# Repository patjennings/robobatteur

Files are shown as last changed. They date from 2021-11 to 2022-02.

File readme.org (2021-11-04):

* Robobatteur
** Principes
   Suite au travail sur la première version du robobatteur, qui effectuait un simple "poum-tchac", j'ai réfléchi à une version plus évoluée.

   La principale évolution sera de pouvoir contrôler le robot à partir d'une séquence midi. Un séquenceur MIDI jouera une partition, et enverra à mesure qu'elle joue des messages aux moteurs. Voici le schéma de principe : sur la ligne du haut, les éléments par lesquels le message passe, sur celle du bas, le message

   #+begin_src text
Ordi -------> Midi out (carte son) --> Midi in (circuit) --> carte Arduino -------------------> circuit --> servomoteur
Note MIDI -------------------------------------------------> routage / instructions de frappe ------------> frappe
   #+end_src

   Cela engendre une autre modification sur la machine, afin de pouvoir assurer la frappe sur des tempos élevés. 2 moteurs par élément, qui farppent alternativement.

   Chaque note correspond à un élément. La note 30 (Do 1) correspond à la grosse caisse, la note 32 à la caisse claire, etc. Les notes sont récapitulées dans le tableau ci-dessous.

   J'ai prévu de pouvoir contrôler quatre éléments de batterie.
   
   | Note MIDI | Note | Élément |
   |-----------+------+---------|
   |        43 | G1   | Ride    |
   |        42 | F1   | Hi-hat  |
   |        38 | D1   | Snare   |
   |        36 | C1   | Kick    |
   
   On s'appuie toujours sur une carte Arduino Uno pour effectuer ce travail.
   
** Circuit
   Plusieurs besoins pour le circuit :
   - un midi in
   - une alimentation par groupe de servos dédiés (les servos ont besoin chacun d'une intensité d'un ampère pour fonctionner correctement. Comme il est difficile de se procurer du 5V 8A, pour pallier à cela, on n'alimente que deux moteurs avec une seule alim 5v à 2a).

   J'ai utilisé une perfboard pour le circuit du module de MIDI In et pour le câblage des servo moteurs, et une autre board pour les circuits d'alim des servos. J'ai fait ça à mesure que j'avancais, j'imagine qu'il y a moyen d'optimiser ça.

   Comme je l'ai mentionné plus haut, j'ai besoin de taper sur quatre éléments de batterie : j'aurai donc besoin de huit servomoteurs.

   #+html: <img src="docs/robobatteur_bb.jpg" width="100%"/>
   
** Menuiserie, disposition
   Principe général. Tout sur un socle, qu'on peut lester avec des parpaings. La disposition reprend celle d'une batterie jouée par un humain, à savoir grosse caisse au milieu, et charleston et caisse claire de part et d'autre.
   Mais on peut être plus ambitieux et disposer ses éléments dans l'espace : après tout, on est seulement limité par la longueur de câble
   Bras dont on peut modifier la rotation, afin de pouvoir effectuer des ajustements fins, pour avoir une frappe assez sonore.
   
   Fixation des servos : baguette en pin (16mm), percé pour recevoir le moteur. Fixation avec des vis
   Fixation des baguettes : perçage, puis fixation avec vis dans le bras de chaque servo
   
   Le circuit et la carte sont fixés dans une boîte, d'où partent les câbles vers les servos (8 groupe de 3 câbles ― phase, neutre, message arduino (?))

   Les câbles sont fixés. C'est encore à l'état de prototype "early", et la robustesse de connexions est le prochain point que je compte améliorer.
   
** Code
   Le code est relativement simple. Les variables sur lesquelles on jouera en fonction du montage sont dans initPos[]. L'angle de rotation de chaque baguette est défini par rotationAngle. On pourra peut-être jouer avec. J'ai peu testé, mais on gagne peut-être en puissance. Le code se répète pas mal, et il pourrait aisément être factorisé. Cela est dû à mes compétences limitées. Malgré tout, le code est sûrement plus lisible pour des novices qui tâcheraient de comprendre ce qui se passe.

*** Librairies externes
    Le programme s'appuie sur les librairies ~MIDI~ et ~Servo~.

    Comment les télécharger ? Le plus simple est d'utiliser l'IDE Arduino, est d'installer les modules via le menu ~Menu~.

    #+html: <img src="docs/lib-install.png"/>

    La librairie ~MIDI~
    #+html: <img src="docs/lib-midi.png"/>

    La librairie ~Servo~
    #+html: <img src="docs/lib-servo.png"/>
    
    Une fois installées, on appelle les librairies dans le code :

    #+begin_src c
     #include <MIDI.h>  // Add Midi Library
     #include <Servo.h> // Add servo lib
    #+end_src

** Fichiers MIDI
   Les fichiers MIDI sont créés avec ~Rosegarden~. J'ai pu tester avec des (croches, doubles-croches) à un tempo de (combien) ?
   
** Setup informatique
   ~QJackCtl~ + ~a2jmidid~ + ~Rosegarden~

   J'utilise Linux Mint. Le setup sera à adapter en fonction de l'OS, et sera sûrement plus simple dans d'autres environnements. Quoi qu'il en soit, voici le mien :

   Les applications utilisées sont :
   - ~QJackCtl~ pour piloter la carte son et effectuer les connexions
   - ~a2jmidid~ pour envoyer des messages MIDI via la carte son
   - ~Rosegarden~ pour créer et lire les fichiers MIDI

   Rosegarden ferta tourner les séquences midi, et enverra les notes vers la carte son via ~QJackCtl~ et ~a2jmidid~ (qui permet à ~QJackCtl~ de piloter les connexions midi).

   #+begin_src bash
     sudo apt-get update
     sudo apt-get install -y qjackctl a2jmidid rosegarden
   #+end_src
   
   Une carte son (/Presonus Audibox44VSL/ pour ma part) est connectée en USB à l'ordinateur.
   
   Ensuite, ~QJackCtl~ est démarré. Si tout roule, on peut lancer ~a2jmidid~

   #+begin_src bash
     a2jmidid -e
   #+end_src

   Si tout fonctionne, on doit voir quelque chose comme ça

   #+begin_src bash
   Retour terminal
   #+end_src

   Puis on peut démarrer ~Rosegarden~

   Une fois que tout est démarré, on revient dans les connexions de ~Qjack~ pour vérifier que ~RoseGarden~ envoie des messages vers le midi out de la carte son (grâce à ~a2jmidid~)

   Si tout fonctionne correctement, une note lue sur ~Rosegarden~ doit activer les servo moteurs

** Améliorer
   Précision des fixations  : angle de fixation des baguettes et des servos aléatoires, ce qui nuit à l'exactitude du tempo (rubato).
   
** Matériel
- Assortiment de fils : <https://www.lextronic.fr/assortiment-fils-de-cablage-monobrin-30m-62595.html>
- Perfboard : <https://www.lextronic.fr/plaque-a-pastilles-cuivrees-81x51-mm-31761.html>
- Condensateur 100 µF <https://www.lextronic.fr/condensateur-chimique-radial-1000uf-35v-58165.html#/condensateurs_85-100f_10v>
- Embase 5v : <https://www.lextronic.fr/embase-d-alimentation-2-1x5-5mm-2529.html>
- Embase DIN : me souviens plus
- Alimentation : 5v 2a (chez RS Composants)
- Servo moteur MG996R : <https://www.miniplanes.fr/servos/tower-pro/mg-996-servo-numerique-pignons-metaux-10kgcm-tower-pro-p-19942.html>
- Résistance 220 ohms + 4.7kohms
- Diode : 1n914 ou 1n4148 <https://composant-electronique.fr/diode-1n4148>
- Optocoupleur 6n138 : <https://composant-electronique.fr/optocoupleur-6n138>

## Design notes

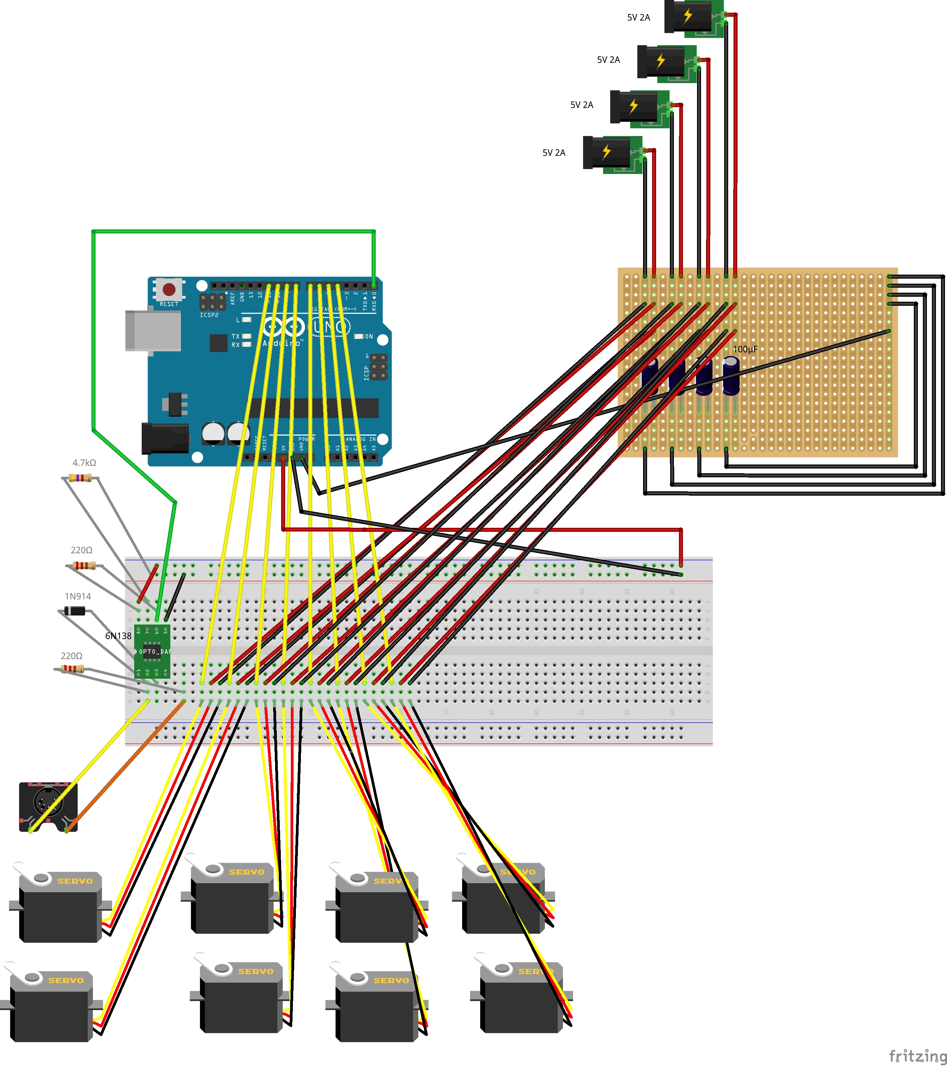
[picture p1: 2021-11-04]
docs/robobatteur_bb.jpg

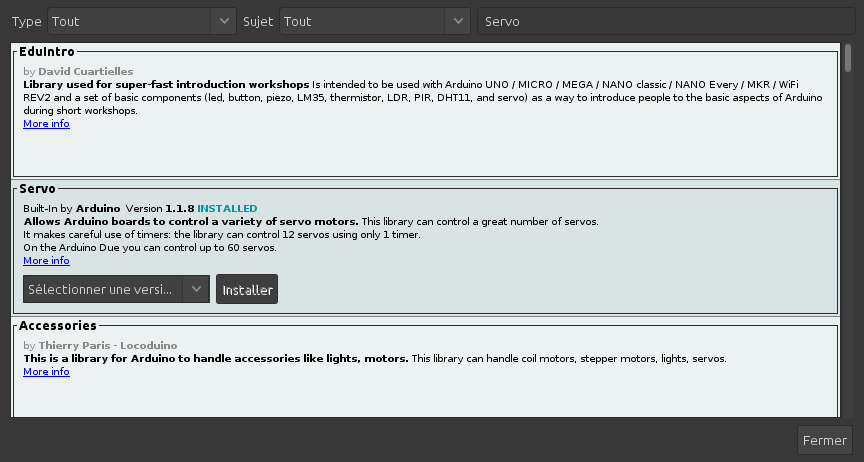
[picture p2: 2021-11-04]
docs/lib-servo.png

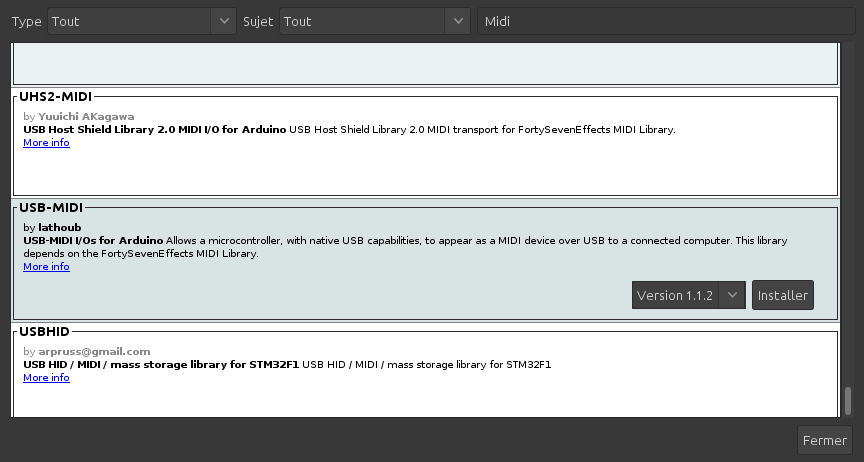
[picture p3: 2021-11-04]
docs/lib-midi.png

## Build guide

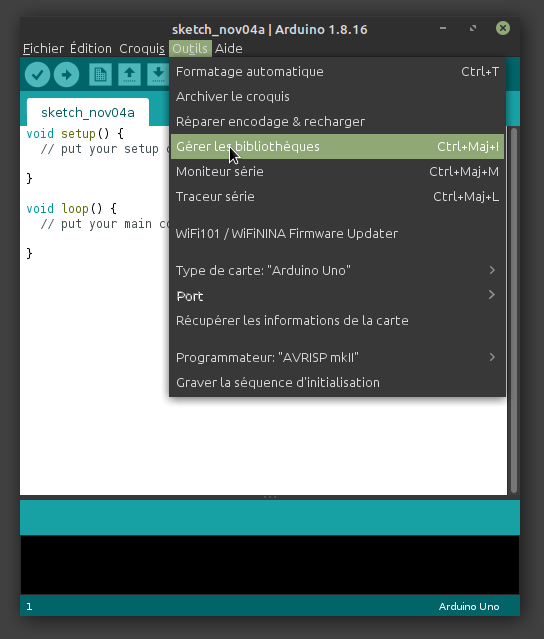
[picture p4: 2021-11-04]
docs/lib-install.png

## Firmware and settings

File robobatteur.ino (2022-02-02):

#include <MIDI.h>  // Add Midi Library
#include <Servo.h> // Add servo lib

#define LED 13    // Arduino Board LED is on Pin 13
Servo srvKick1, srvKick2, srvSnare1, srvSnare2, srvHh1, srvHh2, srvRide1, srvRide2;  // on crée les servos
int initPos[] = {150, 153, 170, 170, 180, 178, 168, 170}; // position initiale des servos, dans l'ordre de déclaration présent ci-avant

int rotationAngle = 45; // coefficient de rotation

boolean toggleSnare = true;
boolean toggleHH = true;
boolean toggleKick = true;
boolean toggleRide = true;

MIDI_CREATE_DEFAULT_INSTANCE();

void setup() {
  pinMode (LED, OUTPUT);
  MIDI.begin(MIDI_CHANNEL_OMNI);
  MIDI.setHandleNoteOn(MyHandleNoteOn);
  MIDI.setHandleNoteOff(MyHandleNoteOff);
  Serial.begin(31250);


  // sorties 1 & 2
  srvKick1.attach(11); // kick 1
  srvKick1.write(initPos[0]);

  srvKick2.attach(10); // kick 2
  srvKick2.write(initPos[1]);

  // sorties 3 & 4
  srvSnare1.attach(9); // snare 1
  srvSnare1.write(initPos[2]);
  
  srvSnare2.attach(8); // snare 2
  srvSnare2.write(initPos[3]);

  // sorties 5 & 6
  srvHh1.attach(7); // hh 1
  srvHh1.write(initPos[4]);
  
  srvHh2.attach(6); // hh 2
  srvHh2.write(initPos[5]);

  // sortie 7 & 8
  srvRide1.attach(5); // misc 1
  srvRide1.write(initPos[6]);

  srvRide2.attach(4); // misc 2
  srvRide2.write(initPos[7]);
}

void loop() { // Main loop
  MIDI.read();
}

void MyHandleNoteOn(byte channel, byte pitch, byte velocity) {
  digitalWrite(LED,HIGH);
  Serial.write("midi spotted");

  // int rotAng = map(velocity, 0, 127, 35, 45);
  int rotAng = 45;

  // c'est ici qu'on décide quelle note active quel moteur
//  if(pitch == 36){  // DO 1
//    hitKick(rotAng);
//  }
//  if(pitch == 38){  // RE 1
//    hitSnare(rotAng);
//  }
//  if(pitch == 42){  // FA#1
//    hitHH(rotAng);
//  }
//  if(pitch == 43){ // SOL 1
//    hitRide(rotAng);
//  }

  if(channel == 9){ hitKick(rotAng); }
  if(channel == 10){ hitSnare(rotAng); }
  if(channel == 13){ hitHH(rotAng); }
  if(channel == 14){ hitRide(rotAng); }
}
void hitKick(int ra){
  if(toggleKick == true){
    srvKick1.write(initPos[0]-ra); // la baguette s'abaisse
    delay(40);
    srvKick1.write(initPos[0]);  // la baguette se relève
    toggleKick = false;
  } else {
    srvKick2.write(initPos[1]-ra); // la baguette s'abaisse
    delay(40);
    srvKick2.write(initPos[1]);  // la baguette se relève
    toggleKick = true;
  }  
  
}
void hitSnare(int ra){
  if(toggleSnare == true){
    srvSnare1.write(initPos[2]-rotationAngle); // la baguette s'abaisse
    delay(40);
    srvSnare1.write(initPos[2]);  // la baguette se relève
    toggleSnare = false;
  } 
  else {
    srvSnare2.write(initPos[3]-rotationAngle); // la baguette s'abaisse
    delay(40);
    srvSnare2.write(initPos[3]);  // la baguette se relève
    toggleSnare = true;
  }
}
void hitHH(int ra){
  if(toggleHH == true){
    srvHh1.write(initPos[4]-ra); // la baguette s'abaisse
    delay(40);
    srvHh1.write(initPos[4]);  // la baguette se relève
    toggleHH = false;
  } else {
    srvHh2.write(initPos[5]-ra); // la baguette s'abaisse
    delay(40);
    srvHh2.write(initPos[5]);  // la baguette se relève
    toggleHH = true;
  }
}
void hitRide(int ra){
  if(toggleRide == true){
    srvRide1.write(initPos[4]-ra); // la baguette s'abaisse
    delay(40);
    srvRide1.write(initPos[4]);  // la baguette se relève
    toggleRide = false;
  } else {
    srvRide2.write(initPos[5]-ra); // la baguette s'abaisse
    delay(40);
    srvRide2.write(initPos[5]);  // la baguette se relève
    toggleRide = true;
  }
}
void MyHandleNoteOff(byte channel, byte pitch, byte velocity) { 
  digitalWrite(LED,LOW);  //Turn LED off
}

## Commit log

2021-10-07 udpate new files
    [robobatteur.fzz]
2021-10-07 format des liens
2021-10-10 update du code > ajout d'un éléméent de batterie. Update du readme (doc)
2021-10-10 modif schéma de principe
2021-10-11 Circuit w/ Fritzing
    [robobatteur.fzz]
2021-10-11 image insertion issue
2021-11-04 Update de la vue du montage Ajout des noms de composants
2021-11-04 update du readme comment installer les librairies, ajout de captures, update du fichier source fritzing
    [robobatteur.fzz]
